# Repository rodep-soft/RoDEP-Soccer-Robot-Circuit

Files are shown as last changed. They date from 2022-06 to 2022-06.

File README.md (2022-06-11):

# RoDEP Soccer Robot's Arduino Shield

## 基板CAD
Eagle

## 使用部品
- TB6612FNG x2  
デュアルモータードライバIC  
[購入先リンク](https://akizukidenshi.com/catalog/g/gI-11317/)
- PCF8574N x1  
Ｉ／Ｏエキスパンダー　ＰＣＦ８５７４Ｎ  
[購入先リンク](https://akizukidenshi.com/catalog/g/gI-13522/)
- MCP3008 x1  
１０ｂｉｔ　８ｃｈ　ＡＤコンバータ　ＭＣＰ３００８－Ｉ／Ｐ  
[購入先リンク](https://akizukidenshi.com/catalog/g/gI-09485/)
- ＩＣソケット（１６Ｐ）x1  
[購入先リンク](https://akizukidenshi.com/catalog/g/gP-00007/)
- ターミナルブロック　２Ｐ　緑　縦　小 x4  
[購入先リンク](https://akizukidenshi.com/catalog/g/gP-02333/)
- 表面実装用タクトスイッチ　ＴＳ－０６１０４ x1  
[購入先リンク](https://akizukidenshi.com/catalog/g/gP-15969/)
- 電解コンデンサー１０μＦ５０Ｖ８５℃　ルビコンＰＫ x2  
[購入先リンク](https://akizukidenshi.com/catalog/g/gP-03116/)
- チップ積層セラミックコンデンサー　０.１μＦ５０Ｖ　Ｆ　１６０８　（４０個入）x5  
[購入先リンク](https://akizukidenshi.com/catalog/g/gP-13374/)
- XHコネクタ3ピン　ポスト x16  
[秋月互換品](https://akizukidenshi.com/catalog/g/gC-17151/)  
[JST純正](https://order.jst-mfg.com/InternetShop/app/index?back=2&product=67526000&jgcd=0&view=ProductDetail)
- XHコネクタ4ピン　ポスト x1
[秋月互換品](https://akizukidenshi.com/catalog/g/gC-17152/)
- 0603サイズのチップ型抵抗10kΩ

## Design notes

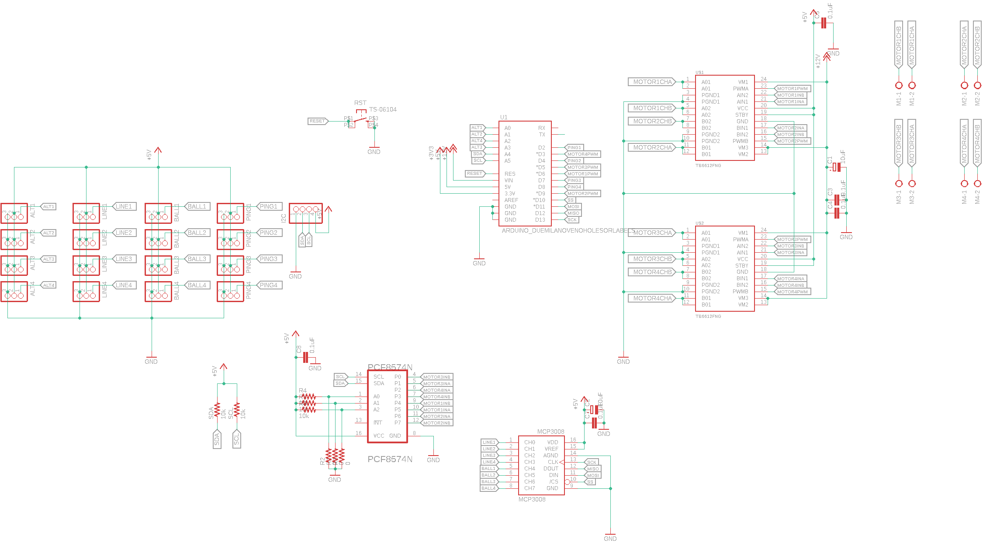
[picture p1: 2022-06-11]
Arduino-Shield.png

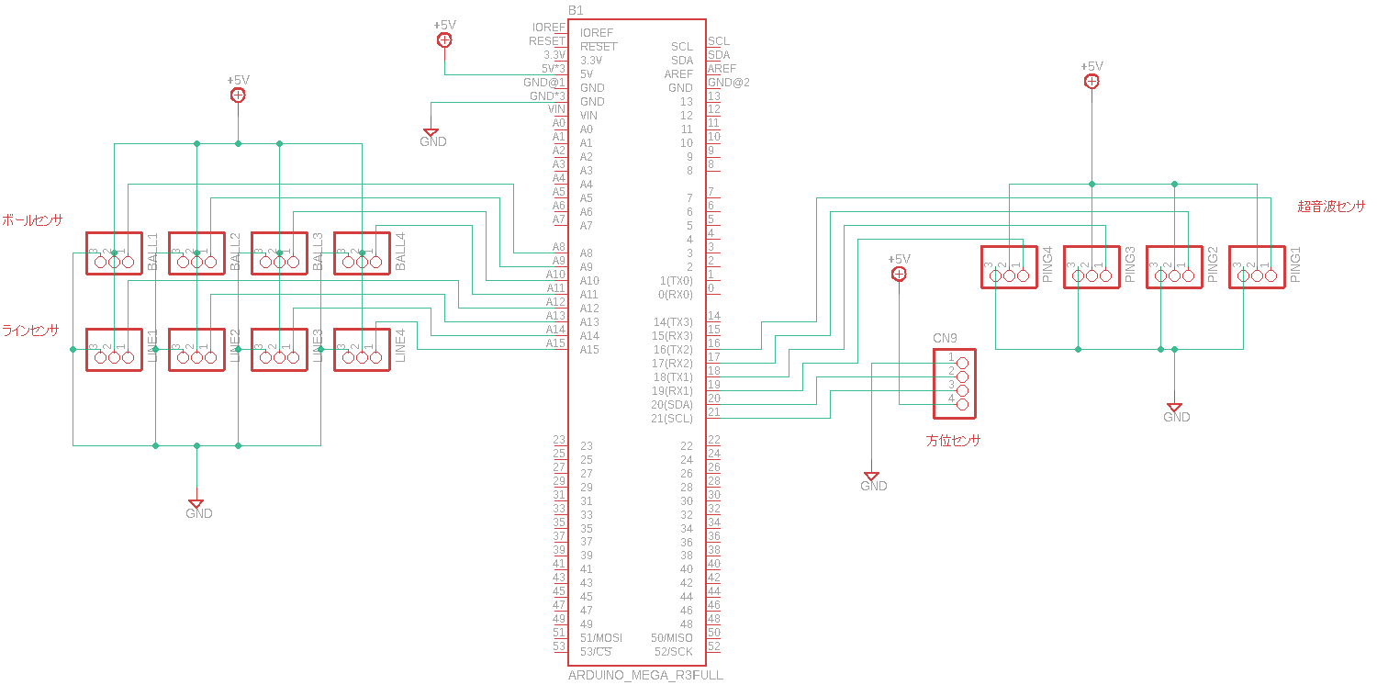
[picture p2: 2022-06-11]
Adafruit-Shield.png

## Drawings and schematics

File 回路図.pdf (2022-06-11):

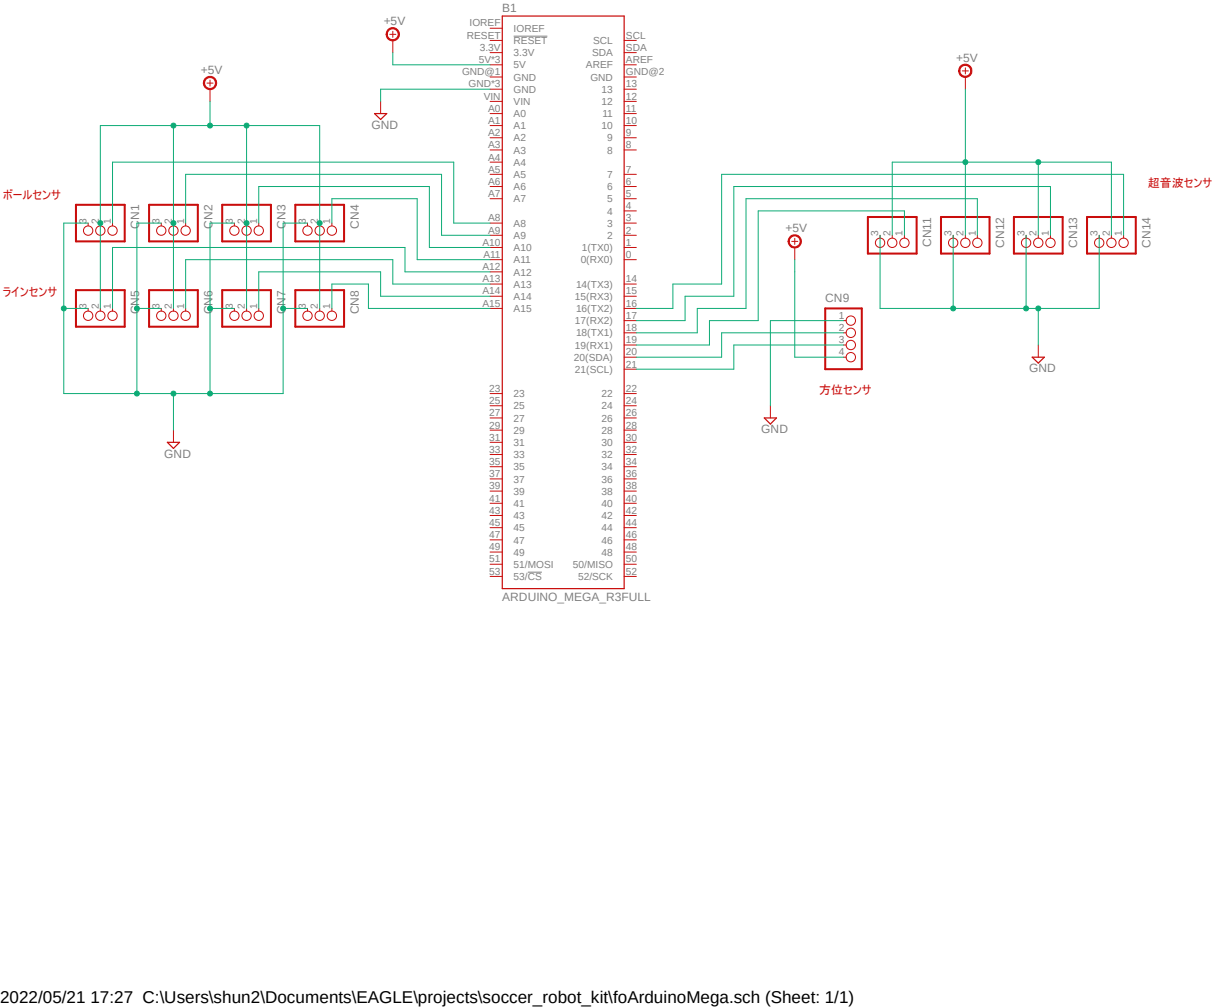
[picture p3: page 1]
ARDUINO_MEGA_R3FULL; GND; RESET RESET; GND GND*3; 52/SCK; 52 51/MOSI 51; 50/MISO; AREF; 21(SCL); 21 20(SDA); VIN VIN; GND@2 GND GND@1; SDA; SDA SCL; SCL IOREF IOREFB1; ボールセンサ; ラインセンサ; 超音波センサ; 方位センサ

2022/05/21 17:27 C:\Users\shun2\Documents\EAGLE\projects\soccer_robot_kit\foArduinoMega.sch (Sheet: 1/1)

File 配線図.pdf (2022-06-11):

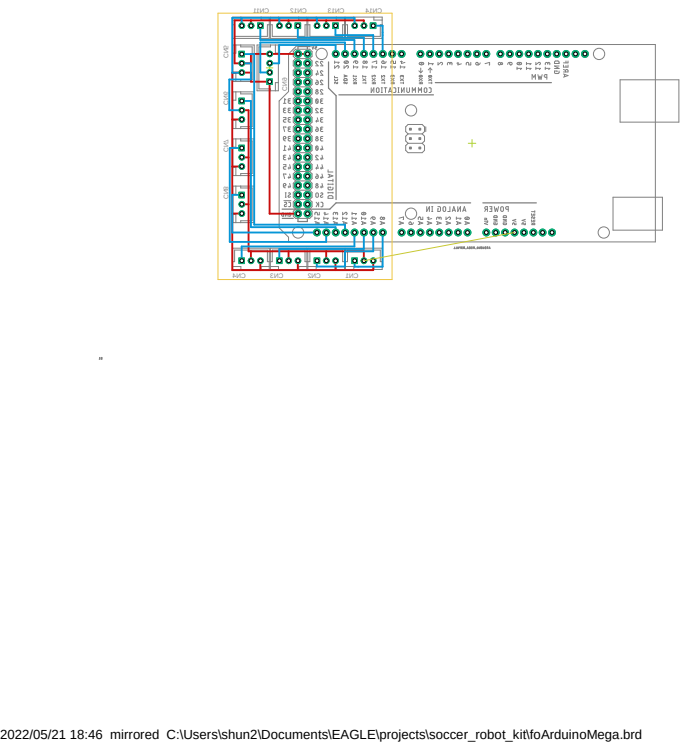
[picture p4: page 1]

2022/05/21 18:46 mirrored C:\Users\shun2\Documents\EAGLE\projects\soccer_robot_kit\foArduinoMega.brd

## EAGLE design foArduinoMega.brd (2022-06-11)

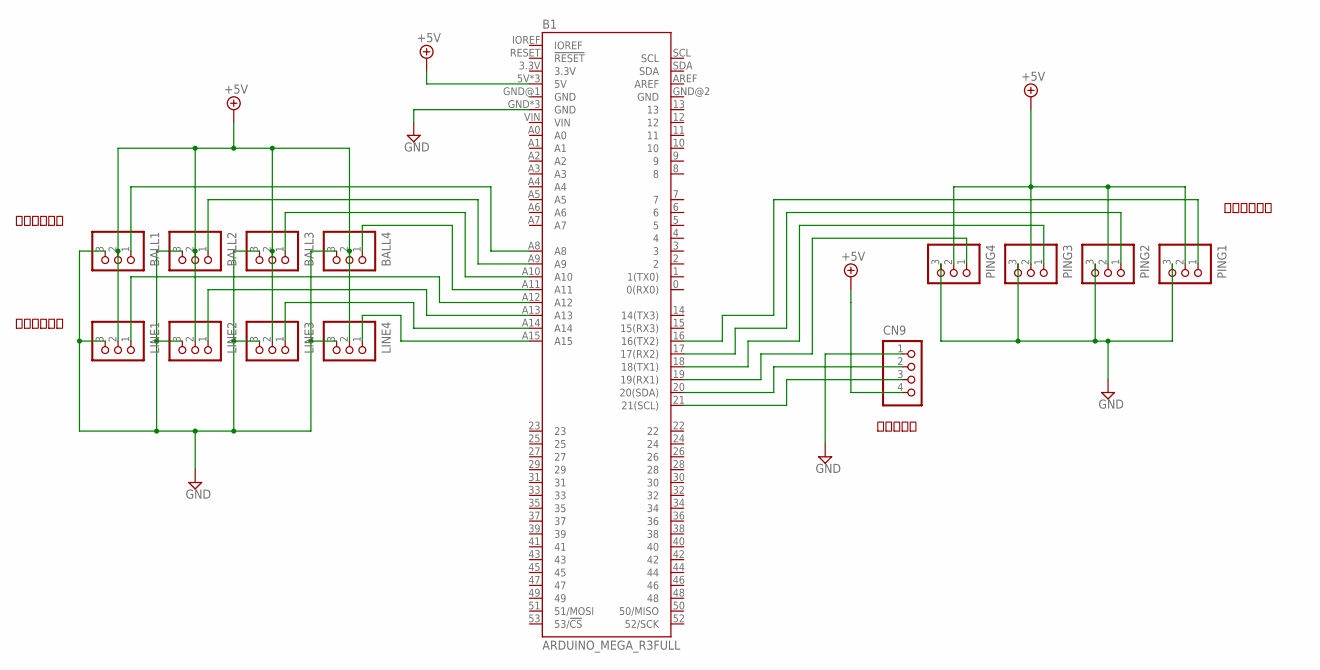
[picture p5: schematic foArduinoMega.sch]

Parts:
B1: ARDUINO_MEGA_R3FULL; ARDUINO_MEGA_NO_SILK
BALL1, BALL2, BALL3, BALL4: B3B-XH-A
CN9: B4B-XH-A
LINE1, LINE2, LINE3, LINE4: B3B-XH-A
PING1, PING2, PING3, PING4: B3B-XH-A

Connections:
+5V: B1.5V, B1.5V@1 (5V), B1.5V@2 (5V), BALL1.2, BALL2.2, BALL3.2, BALL4.2, CN9.4, LINE1.2, LINE2.2, LINE3.2, LINE4.2, PING1.2, PING2.2, PING3.2, PING4.2
GND: B1.GND, B1.GND@3 (GND), B1.GND@4 (GND), BALL1.3, BALL2.3, BALL3.3, BALL4.3, CN9.1, LINE1.3, LINE2.3, LINE3.3, LINE4.3, PING1.3, PING2.3, PING3.3, PING4.3
unnamed: B1.A11, BALL4.1
unnamed: B1.A10, BALL3.1
unnamed: B1.A9, BALL2.1
unnamed: B1.A8, BALL1.1
unnamed: B1.A15, LINE4.1
unnamed: B1.A14, LINE3.1
unnamed: B1.A13, LINE2.1
unnamed: B1.A12, LINE1.1
unnamed: B1.21 (21(SCL)), CN9.3
unnamed: B1.20 (20(SDA)), CN9.2
unnamed: B1.17 (17(RX2)), PING2.1
unnamed: B1.16 (16(TX2)), PING1.1
unnamed: B1.19 (19(RX1)), PING4.1
unnamed: B1.18 (18(TX1)), PING3.1

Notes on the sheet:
ボールセンサ
ラインセンサ
超音波センサ
方位センサ

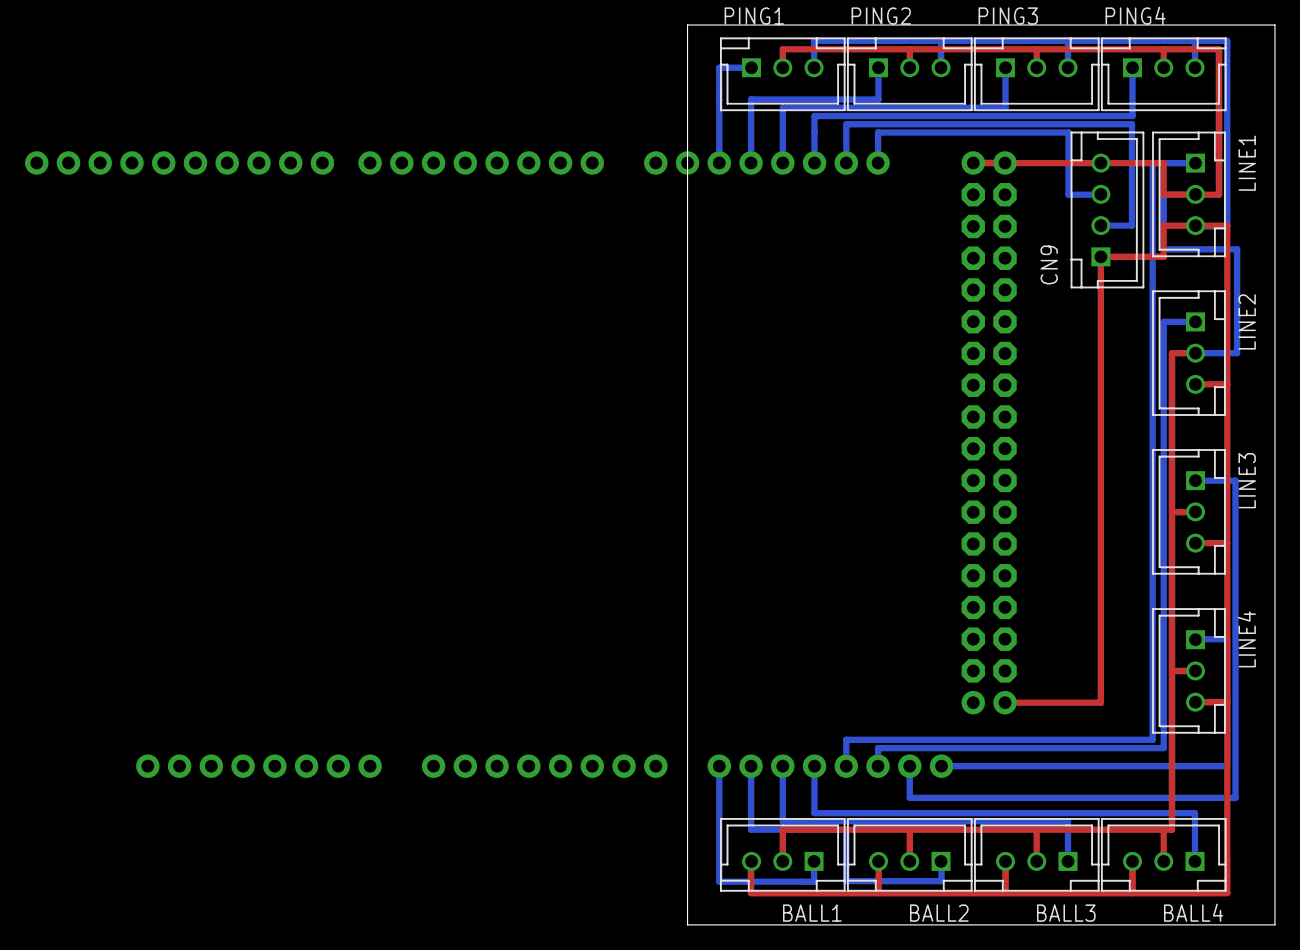
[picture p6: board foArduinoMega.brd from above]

Board: 2 copper layers, 47.0 x 72.0 mm, 14 parts (0 on the bottom side), 16 nets.

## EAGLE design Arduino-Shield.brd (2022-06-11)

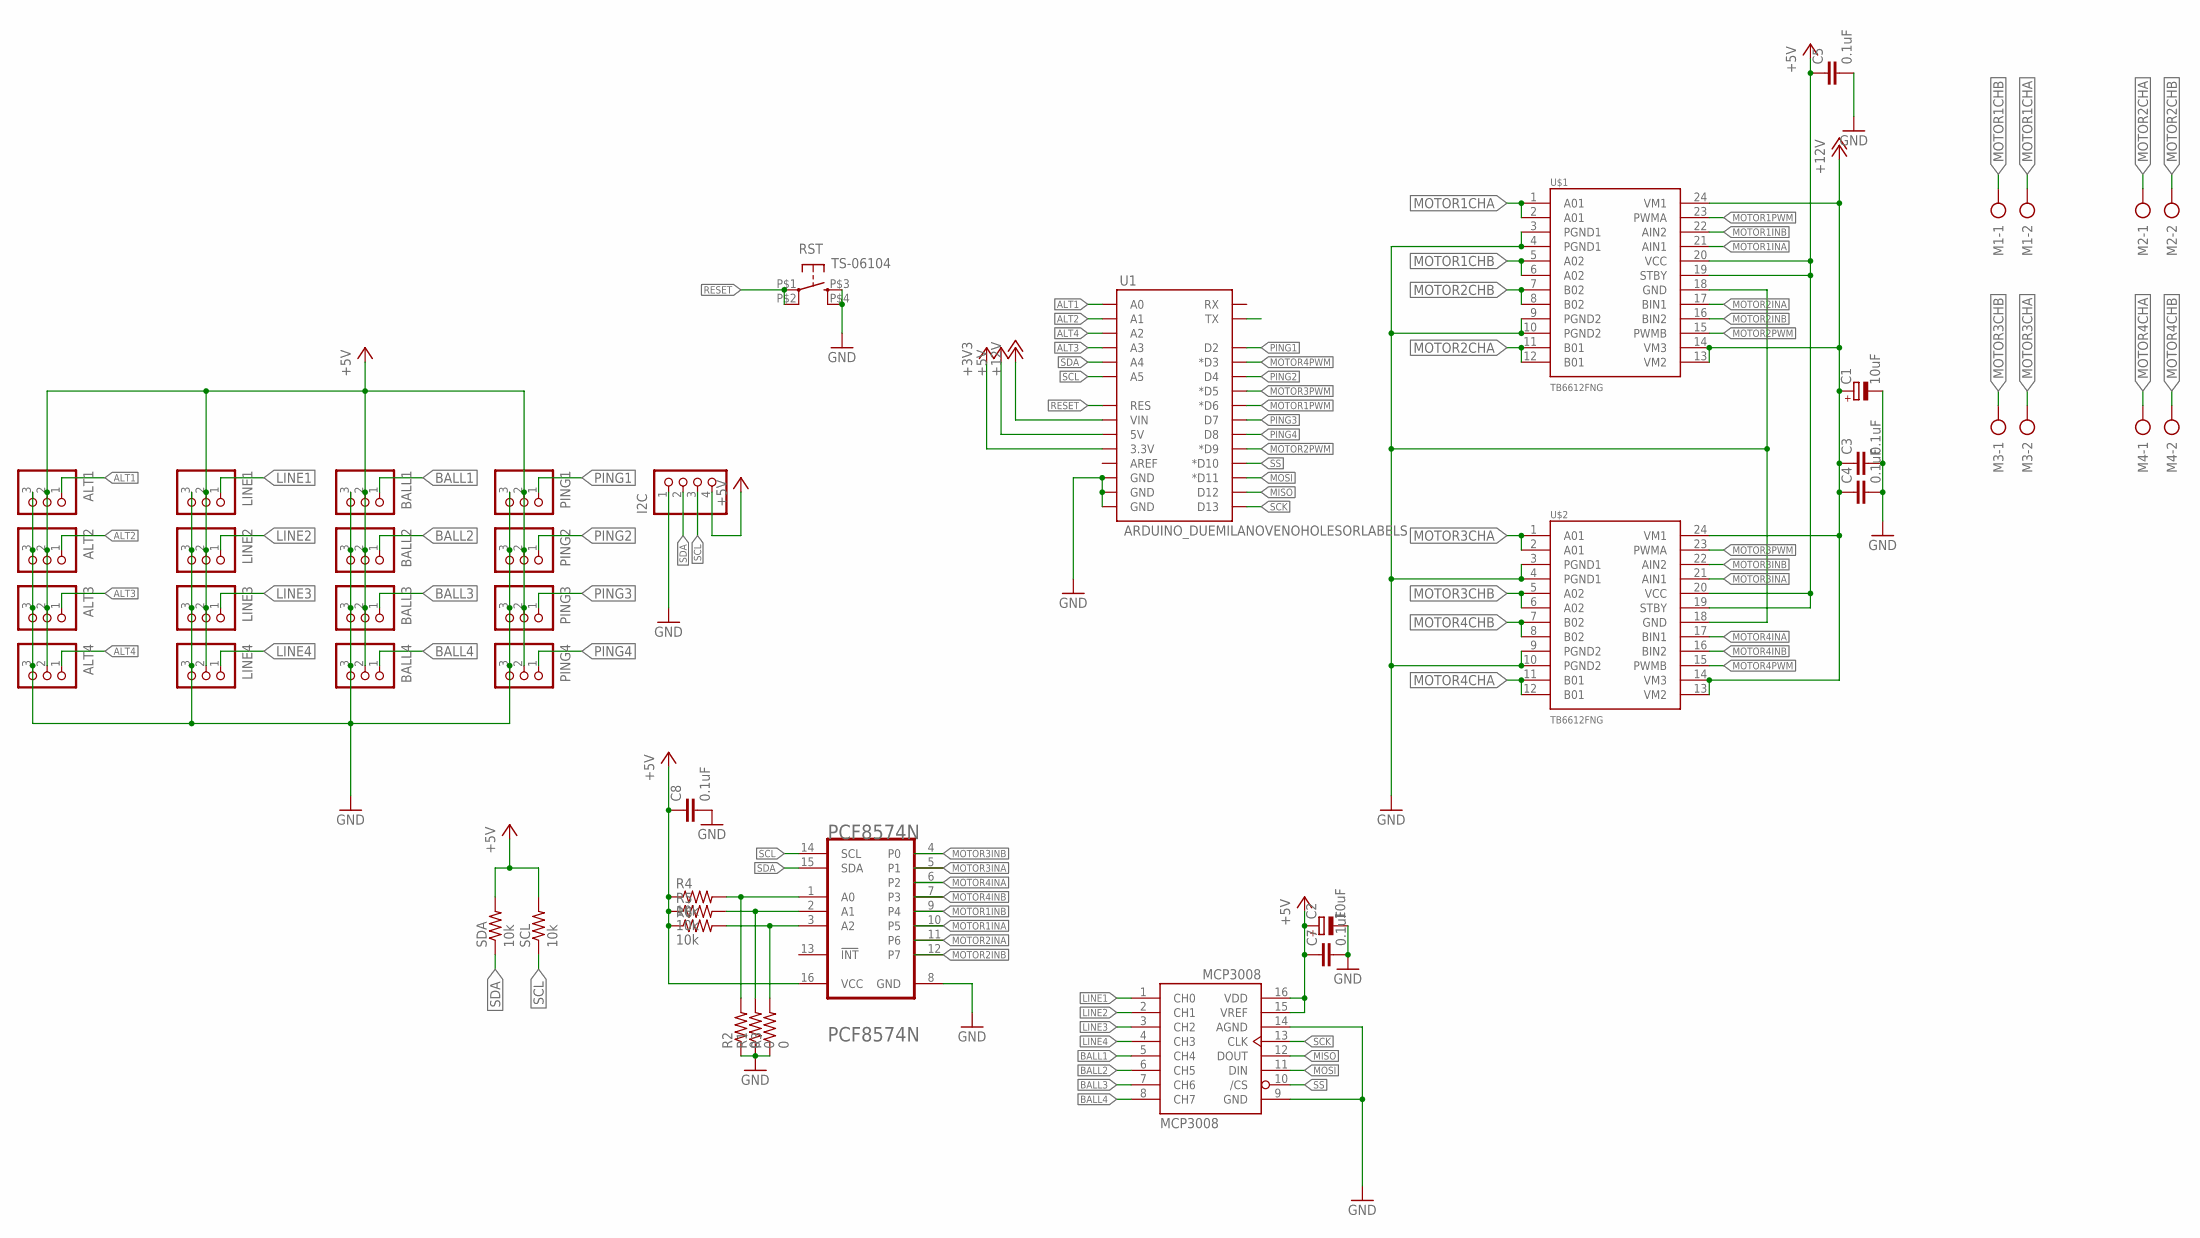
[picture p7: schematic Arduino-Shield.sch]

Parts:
ALT1, ALT2, ALT3, ALT4: B3B-XH-A
BALL1, BALL2, BALL3, BALL4: B3B-XH-A
C1, C2: 10uF; E2-5
C3, C4, C5, C7, C8: 0.1uF; C1608
I2C: B4B-XH-A
LINE1, LINE2, LINE3, LINE4: B3B-XH-A
M1, M2, M3, M4: AK500/2-H
MCP3008: MCP3008; DIL16
PCF8574N: TEXAS_INSTRUMENTS_PCF8574NTEXAS_INSTRUMENTS_PCF85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; TEXAS_INSTRUMENTS_PCF8574N_0
PING1, PING2, PING3, PING4: B3B-XH-A
R1, R2, R3: 0; M2012
R4, R5, R6: 10k; R0603
RST: TS-06104
SCL: 10k; R0603
SDA: 10k; R0603
U1: ARDUINO_DUEMILANOVENOHOLESORLABELS; DUEMILANOVE_SHIELD_NOHOLES_NOLABELS
U$1, U$2: TB6612FNG; SSOP24

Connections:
+3V3: U1.3.3V
+5V: ALT1.2, ALT2.2, ALT3.2, ALT4.2, BALL1.2, BALL2.2, BALL3.2, BALL4.2, C2.+, C5.1, C7.1, C8.1, I2C.4, LINE1.2, LINE2.2, LINE3.2, LINE4.2, MCP3008.15 (VREF), MCP3008.16 (VDD), PCF8574N.16 (VCC), PING1.2, PING2.2, PING3.2, PING4.2, R4.1, R5.1, R6.1, SCL.2, SDA.2, U1.5V, U$1.19 (STBY), U$1.20 (VCC), U$2.19 (STBY), U$2.20 (VCC)
+12V: C1.+, C3.1, C4.1, U1.VIN, U$1.13 (VM2), U$1.14 (VM3), U$1.24 (VM1), U$2.13 (VM2), U$2.14 (VM3), U$2.24 (VM1)
ALT1: ALT1.1, U1.A0
ALT2: ALT2.1, U1.A1
ALT3: ALT3.1, U1.A3
ALT4: ALT4.1, U1.A2
BALL1: BALL1.1, MCP3008.5 (CH4)
BALL2: BALL2.1, MCP3008.6 (CH5)
BALL3: BALL3.1, MCP3008.7 (CH6)
BALL4: BALL4.1, MCP3008.8 (CH7)
GND: ALT1.3, ALT2.3, ALT3.3, ALT4.3, BALL1.3, BALL2.3, BALL3.3, BALL4.3, C1.-, C2.-, C3.2, C4.2, C5.2, C7.2, C8.2, I2C.1, LINE1.3, LINE2.3, LINE3.3, LINE4.3, MCP3008.9 (GND), MCP3008.14 (AGND), PCF8574N.8 (GND), PING1.3, PING2.3, PING3.3, PING4.3, R1.1, R2.1, R3.1, RST.P$3 (3), RST.P$4 (4), U1.GND@0 (GND), U1.GND@1 (GND), U1.GND@2 (GND), U$1.3 (PGND1), U$1.4 (PGND1), U$1.9 (PGND2), U$1.10 (PGND2), U$1.18 (GND), U$2.3 (PGND1), U$2.4 (PGND1), U$2.9 (PGND2), U$2.10 (PGND2), U$2.18 (GND)
LINE1: LINE1.1, MCP3008.1 (CH0)
LINE2: LINE2.1, MCP3008.2 (CH1)
LINE3: LINE3.1, MCP3008.3 (CH2)
LINE4: LINE4.1, MCP3008.4 (CH3)
MISO: MCP3008.12 (DOUT), U1.D12
MOSI: MCP3008.11 (DIN), U1.D11 (*D11)
MOTOR1CHA: M1.2, U$1.1 (A01), U$1.2 (A01)
MOTOR1CHB: M1.1, U$1.5 (A02), U$1.6 (A02)
MOTOR1INA: PCF8574N.10 (P5), U$1.21 (AIN1)
MOTOR1INB: PCF8574N.9 (P4), U$1.22 (AIN2)
MOTOR1PWM: U1.D6 (*D6), U$1.23 (PWMA)
MOTOR2CHA: M2.1, U$1.11 (B01), U$1.12 (B01)
MOTOR2CHB: M2.2, U$1.7 (B02), U$1.8 (B02)
MOTOR2INA: PCF8574N.11 (P6), U$1.17 (BIN1)
MOTOR2INB: PCF8574N.12 (P7), U$1.16 (BIN2)
MOTOR2PWM: U1.D9 (*D9), U$1.15 (PWMB)
MOTOR3CHA: M3.2, U$2.1 (A01), U$2.2 (A01)
MOTOR3CHB: M3.1, U$2.5 (A02), U$2.6 (A02)
MOTOR3INA: PCF8574N.5 (P1), U$2.21 (AIN1)
MOTOR3INB: PCF8574N.4 (P0), U$2.22 (AIN2)
MOTOR3PWM: U1.D5 (*D5), U$2.23 (PWMA)
MOTOR4CHA: M4.1, U$2.11 (B01), U$2.12 (B01)
MOTOR4CHB: M4.2, U$2.7 (B02), U$2.8 (B02)
MOTOR4INA: PCF8574N.6 (P2), U$2.17 (BIN1)
MOTOR4INB: PCF8574N.7 (P3), U$2.16 (BIN2)
MOTOR4PWM: U1.D3 (*D3), U$2.15 (PWMB)
unnamed: PCF8574N.1 (A0), R2.2, R4.2
unnamed: PCF8574N.2 (A1), R1.2, R5.2
unnamed: PCF8574N.3 (A2), R3.2, R6.2
PING1: PING1.1, U1.D2
PING2: PING2.1, U1.D4
PING3: PING3.1, U1.D7
PING4: PING4.1, U1.D8
RES2: U1.TX
RESET: RST.P$1 (1), RST.P$2 (2), U1.RES
SCK: MCP3008.13 (CLK), U1.D13
SCL: I2C.3, PCF8574N.14 (SCL), SCL.1, U1.A5
SDA: I2C.2, PCF8574N.15 (SDA), SDA.1, U1.A4
SS: MCP3008.10 (/CS), U1.D10 (*D10)

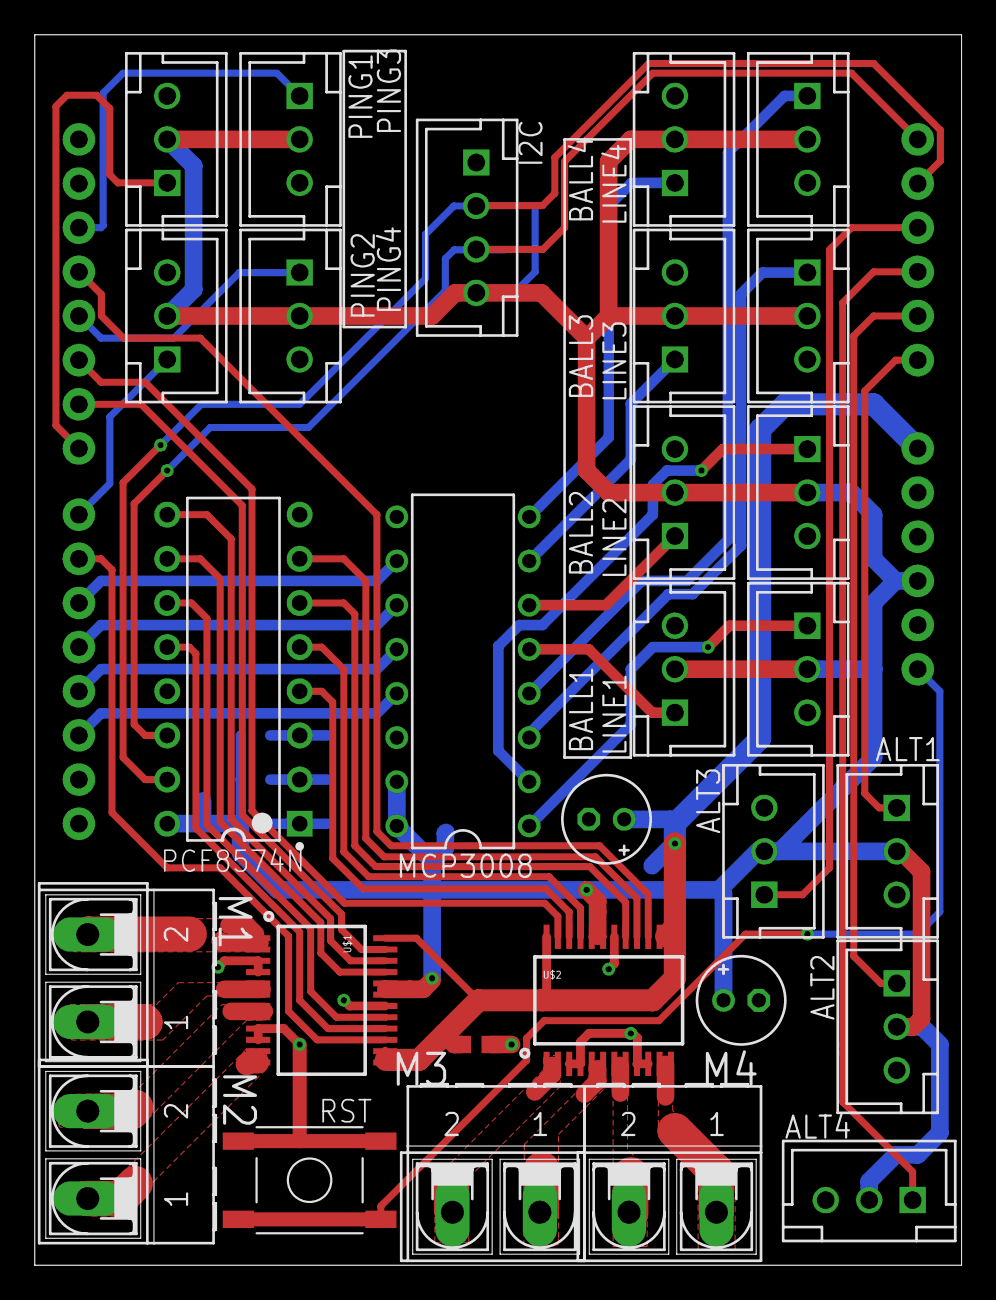
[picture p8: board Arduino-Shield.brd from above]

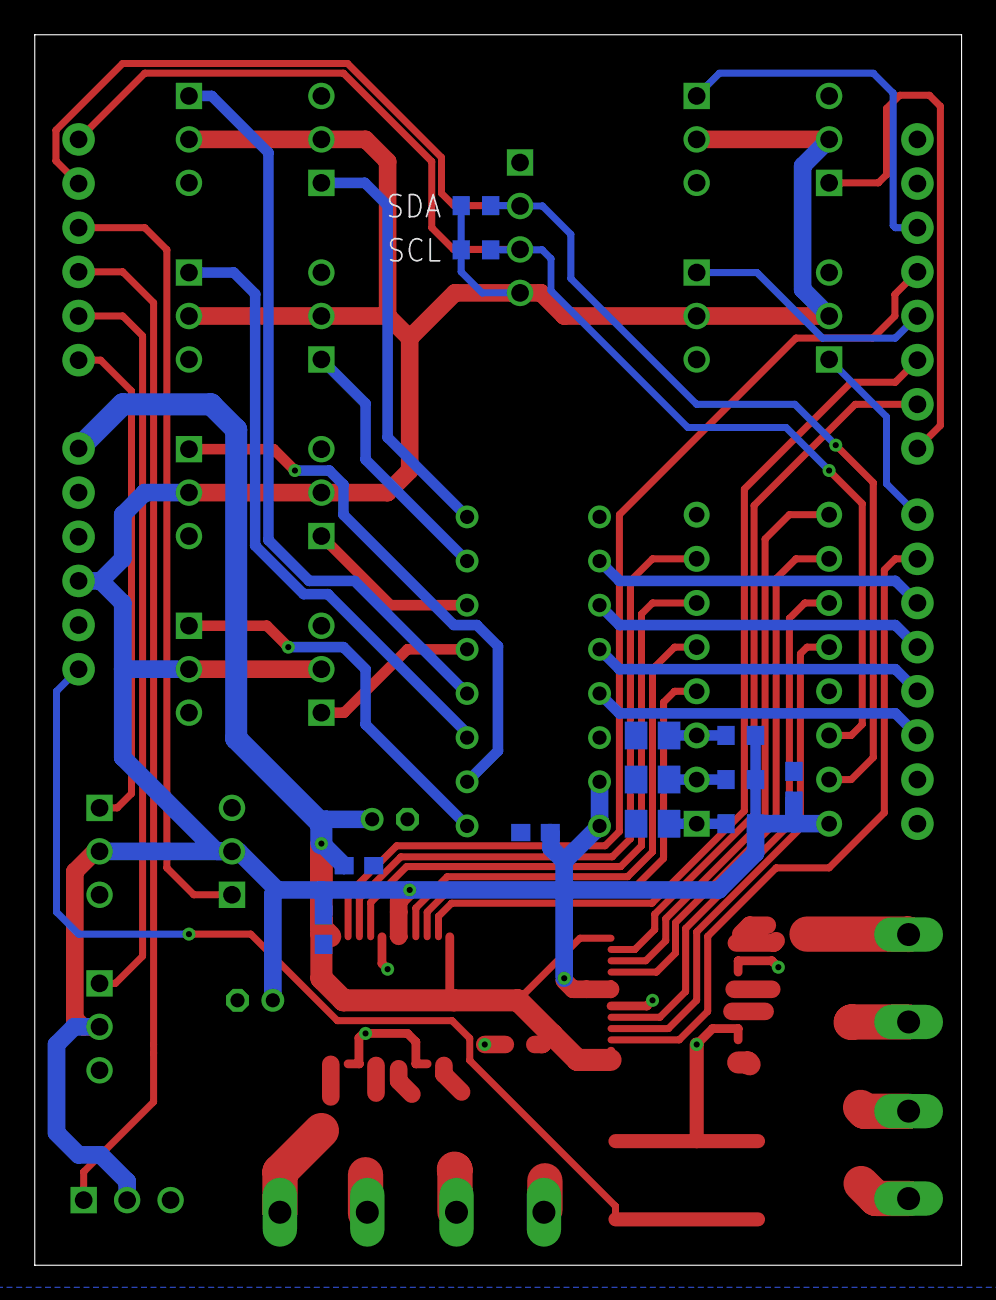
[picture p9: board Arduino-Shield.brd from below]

Board: 2 copper layers, 53.3 x 70.8 mm, 43 parts (13 on the bottom side), 49 nets.

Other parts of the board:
U$3: RODEP2

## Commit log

2022-06-11 #release v1
    [Arduino-Shield.brd, Arduino-Shield.csv, Arduino-Shield.sch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]
2022-06-11 #release Adafruit ciruit
    [foArduinoMega.brd, foArduinoMega.sch]

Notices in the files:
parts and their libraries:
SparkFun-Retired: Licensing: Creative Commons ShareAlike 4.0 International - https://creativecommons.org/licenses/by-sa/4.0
